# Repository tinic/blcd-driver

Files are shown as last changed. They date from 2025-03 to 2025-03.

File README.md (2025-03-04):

# bldc-driver
Motor driver for brushless dc air conditioner motors

This is a PCB design for readily available adjustable brushless motors used in air conditioning units. These units are great since they are sealed and have ajustable speed while using very little power. I used them to drive a stirrer motor to replace the misspecced AC motors (model YYS6-2/110V/60Hz/0.15A) on the otherwise amazing KOMOS KRYO Inline Draft Beer Chillers which tend to fail quickly and generate extreme amounts of heat (~158F/70C measured). Power consumption is reduced from ~17W to around ~4W for my application while staying _completely_ cool. Torque is ecxellent but not exessive in case of obstructions.

The following units have been tested:

140VDC rated (on 120VAC power):
- ZKFP-20-8-113

310VDC rated (on 240VAC power):
- WZDK30-38G

Notes:
- While these units are rated 140/310VDC they work fine with regular rectified AC power (170/338VDC) which makes the implementation simple/cheap.
- The parts used here are complete overkill as this is not designed for mass manufacturing and the price difference with cheaper parts was negligible in single digit units (~$20 with the DigiKey BOM).
- The only special part here is the 15V DC/DC converter as using a couple of LDOs for this application would have caused excessive power use and heat. A constant current source like a capacitive dropper would not have worked either as the power consumption by these motors on the 15V rail is not constant.
- The PCB was designed to stay under 100x100mm to take advantage of flat price of $5 PCBWay offers for these sizes.

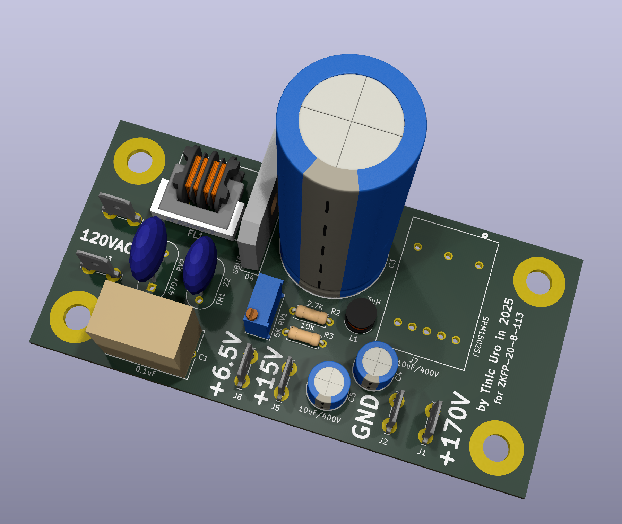
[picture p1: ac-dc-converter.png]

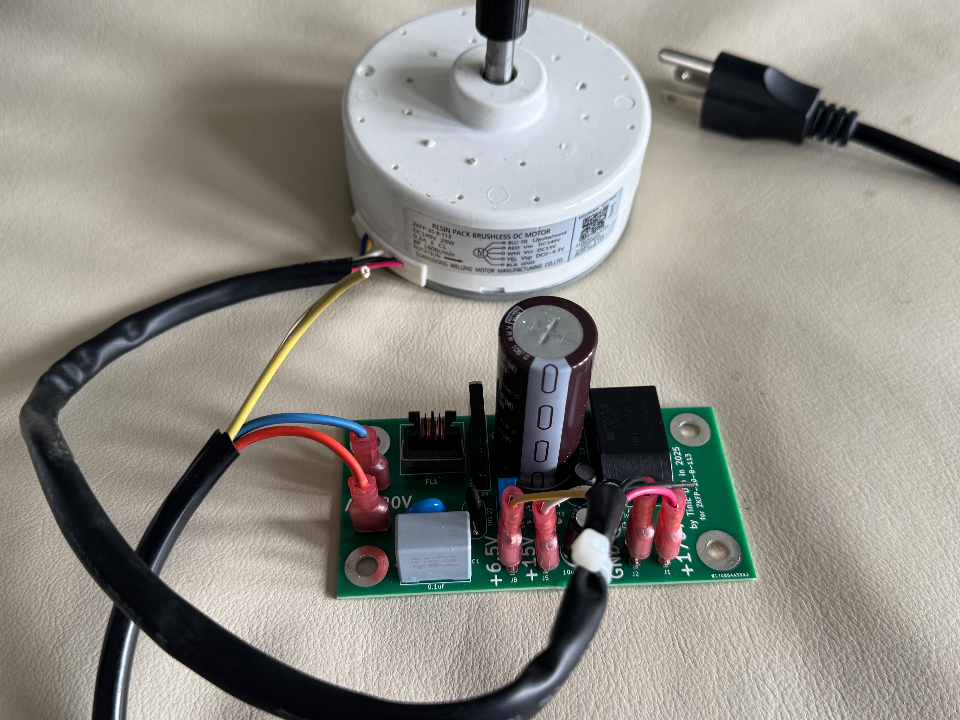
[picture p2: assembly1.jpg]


New motor installed in the beer chiller:

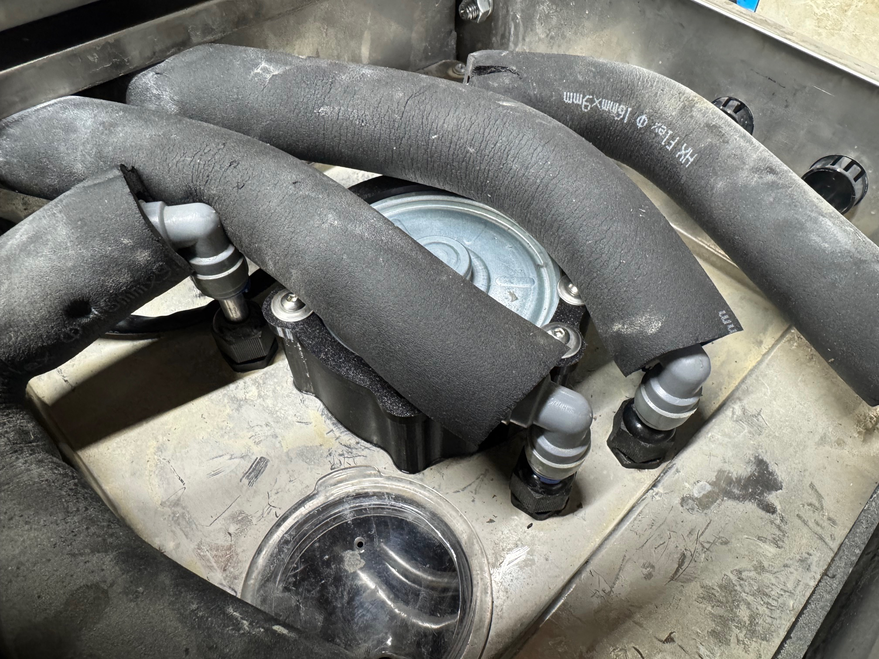
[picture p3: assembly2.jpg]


New stirrer motor with 3d printed blade on the left, old one on the right:

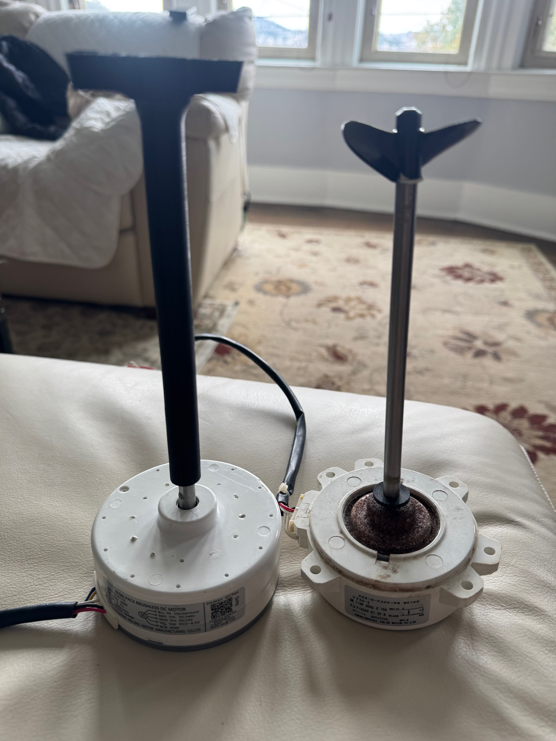
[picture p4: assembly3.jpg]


The push in fittings were completely cooked by the old motor:

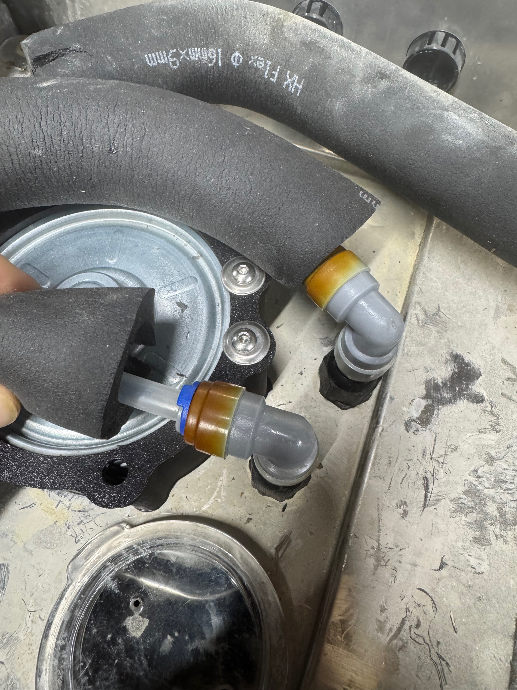
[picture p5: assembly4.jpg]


Full assembly of the new motor in the chiller, the new PCB is on the bottom right:

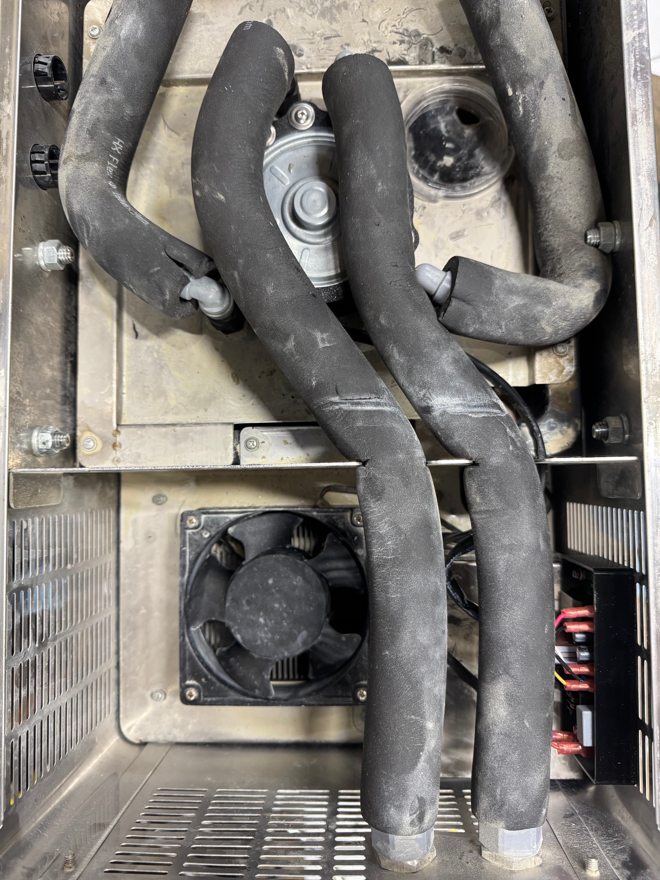
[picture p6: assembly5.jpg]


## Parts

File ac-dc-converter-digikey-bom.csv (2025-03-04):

Country of Origin may be different at time of shipment.
The HTSUS and ECCN information shown is for informational purposes only and is not a representation or warranty as to the accuracy or reliability of these classifications. All information is provided "as is" and is subject to change without notice. Any use made of the information provided is without recourse to Digi-Key and at the user's risk.
Index | Manufacturer Part Number | Manufacturer Name | Description | Availability | Stock Status | Attrition % | Requested Quantity 1 | Pack Quantity 1 | Pack Type 1 | Digi-Key Part Number 1 | Unit Price 1 | Extended Price 1 | Minimum Order Quantity 1 | Customer Reference | Requested Part Number | Lead Weeks | Datasheet | Reference Designator | US Import Tariff | Note | Part Status | RoHS Status | Moisture Sensitivity Level (MSL) | ECCN | HTSUS | Country of Origin | Environmental Information | Original Part numbers | Image | Product Notes
1 | SPM1502SJ | Tamura | DC DC CONVERTER 15V 4W | 301 | In Stock |  | 1 | 1 | Bulk | MT7389-ND | 5.26000 | $5.26 | 1 |  | SPM1502SJ | 26 | https://www.tamuracorp.com/electronics/pdf/EN/SPM/SPM1502SJ_1509CE.pdf |  | May apply on shipments to the U.S. |  | Active | RoHS Compliant | 1 (Unlimited) | EAR99 | 8504.40.9580 | China |  | SPM1502SJ | https://mm.digikey.com/Volume0/opasdata/d220001/medias/images/993/SPM1203SJ.JPG
2 | 400AX10MEFC8X16 | Rubycon | CAP ALUM 10UF 20% 400V RADIAL TH | 3,850 | In Stock |  | 2 | 2 | Bulk | 1189-3119-ND | 0.74000 | $1.48 | 1 |  | 400AX10MEFC8X16 | 16 | https://www.rubycon.co.jp/wp-content/uploads/catalog-aluminum/AX.pdf |  | - |  | Active | ROHS3 Compliant | Not Applicable | EAR99 | 8532.22.0020 | Japan |  | 400AX10MEFC8X16 | https://mm.digikey.com/Volume0/opasdata/d220001/medias/images/1284/AX-SERIES-8x18mm.jpg
3 | 726386-2 | TE Connectivity AMP Connectors | CONN QC TAB 0.250 SOLDER | 38,617 | In Stock |  | 6 | 6 | Bulk | A114371-ND | 0.22000 | $1.32 | 1 |  | 726386-2 | 9 | https://www.te.com/usa-en/product-726386-2.datasheet.pdf |  | - |  | Active | ROHS3 Compliant | 1 (Unlimited) | EAR99 | 8536.90.4000 | Switzerland | http://www.te.com/commerce/alt/SinglePartSearch.do?PN=726386-2&dest=stmt | 726386-2 | https://mm.digikey.com/Volume0/opasdata/d220001/medias/images/29/726386-2.JPG
4 | GBU6M | Diotec Semiconductor | BRIDGE RECT 1PHASE 1KV 4.2A GBU | 884 | In Stock |  | 1 | 1 | Bulk | 4878-GBU6M-ND | 0.83000 | $0.83 | 1 |  | 4878-GBU6M-ND | 2 | https://diotec.com/request/datasheet/gbu6a.pdf |  | May apply on shipments to the U.S. |  | Active | Not applicable | Not Applicable | EAR99 | 8541.10.0080 | China | https://diotec.com/request/imds/p28_e.pdf | 4878-GBU6M-ND | https://mm.digikey.com/Volume0/opasdata/d220001/medias/images/4849/MFG_2796_GBU4A.jpg
5 | MOV-10D471K | Bourns Inc. | VARISTOR 470V 2.5KA DISC 10MM | 66,408 | In Stock |  | 1 | 1 | Bulk | 118-MOV-10D471K-ND | 0.49000 | $0.49 | 1 |  | MOV-10D471K | 13 | https://www.bourns.com/docs/Product-Datasheets/MOV10D.pdf |  | May apply on shipments to the U.S. |  | Active | ROHS3 Compliant | 1 (Unlimited) | EAR99 | 8533.40.4000 | China | https://www.bourns.com/docs/Product-MDS/MOV-10DxxxK.pdf|https://www.bourns.com/docs/rohs-content/bourns-reach-letter.pdf|https://www.bourns.com/docs/rohs-cofc/gmov_cofc.pdf?sfvrsn=c25579f6_4 | MOV-10D471K | https://mm.digikey.com/Volume0/opasdata/d220001/medias/images/405/MFG_MOV-10.jpg
6 | BFC233810104 | Vishay Beyschlag/Draloric/BC Components | CAP FILM 0.1UF 20% 1KVDC RADIAL | 9,153 | In Stock |  | 1 | 1 | Bulk | BC1575-ND | 1.30000 | $1.30 | 1 |  | BFC233810104 | 16 | https://www.vishay.com/docs/28116/mkp3381x1.pdf |  | - |  | Active | ROHS3 Compliant | Not Applicable | EAR99 | 8532.25.0020 | India |  | BFC233810104 | https://mm.digikey.com/Volume0/opasdata/d220001/medias/images/2573/MKP%20338.jpg
7 | SU9HF-07015 | KEMET | CMC 1.5MH 700MA 2LN TH | 773 | In Stock |  | 1 | 1 | Tray | 399-SU9HF-07015-ND | 0.96000 | $0.96 | 1 |  | SU9HF-07015 | 33 | https://search.kemet.com/download/datasheet/SU9HF-07015 |  | - |  | Active | ROHS3 Compliant | Not Applicable | EAR99 | 8504.50.8000 | Vietnam |  | SU9HF-07015 | https://mm.digikey.com/Volume0/opasdata/d220001/medias/images/535/SU9V.jpg
8 | MF72-022D7 | Cantherm | ICL 22 OHM 20% 600MA 9MM | 19,910 | In Stock |  | 1 | 1 | Bulk | 317-1153-ND | 0.43000 | $0.43 | 1 |  | MF72-022D7 | 8 | https://www.cantherm.com/wp-content/uploads/2018/08/MF72_AUG_2018.pdf |  | May apply on shipments to the U.S. |  | Active | ROHS3 Compliant | Not Applicable | EAR99 | 8533.40.8070 | China | https://www.cantherm.com/wp-content/uploads/2017/05/RoHS-3-English-2015-863-EU-SEP-18-2019.pdf | MF72-022D7 | https://mm.digikey.com/Volume0/opasdata/d220001/medias/images/929/MF72-022D7.JPG
9 | EKMM401VSN221MP50S | Chemi-Con | CAP ALUM 400V POLAR | 388 | In Stock |  | 1 | 1 | Bulk | 565-EKMM401VSN221MP50S-ND | 5.43000 | $5.43 | 1 |  | EKMM401VSN221MP50S | 18 | https://www.chemi-con.co.jp/products/relatedfiles/capacitor/catalog/KMMN-e.PDF |  | - |  | Active | ROHS3 Compliant | Not Applicable | EAR99 | 8532.22.0040 | Japan |  | EKMM401VSN221MP50S | https://mm.digikey.com/Volume0/opasdata/d220001/medias/images/3603/EKMGXXXELLXXXMHBXD.jpg
10 | 3296W-1-502LF | Bourns Inc. | TRIMMER 5K OHM 0.5W PC PIN TOP | 514 | In Stock |  | 1 | 1 | Tube | 3296W-502LF-ND | 2.05000 | $2.05 | 1 |  | 3296W-502LF-ND | 10 | https://www.bourns.com/docs/product-datasheets/3296.pdf |  | - |  | Active | ROHS3 Compliant | Not Applicable | EAR99 | 8533.40.8050 | Costa Rica | https://www.bourns.com/docs/rohs-cofc/cofc_trim1.pdf?sfvrsn=ec972807_4 | 3296W-502LF-ND | https://mm.digikey.com/Volume0/opasdata/d220001/medias/images/2383/3296W%20SERIES.jpg
11 | MFR-25FRF52-10K | YAGEO | RES 10K OHM 1% 1/4W AXIAL | 374,500 | In Stock |  | 1 | 1 | Cut Tape (CT) | 13-MFR-25FRF52-10KCT-ND | 0.10000 | $0.10 | 1 |  | 13-MFR-25FRF52-10KTR-ND | 16 | https://www.yageo.com/upload/media/product/app/datasheet/lr/yageo-mfr_datasheet.pdf |  | May apply on shipments to the U.S. |  | Active | ROHS3 Compliant | Not Applicable | EAR99 | 8533.21.0090 | China |  | 13-MFR-25FRF52-10KTR-ND | https://mm.digikey.com/Volume0/opasdata/d220001/medias/images/1206/MFR-25FRF52-10K.jpg
12 | RNMF14FTC2K70 | Stackpole Electronics Inc | RES 2.7K OHM 1% 1/4W AXIAL | 18,090 | In Stock |  | 1 | 1 | Cut Tape (CT) | S2.7KCACT-ND | 0.10000 | $0.10 | 1 |  | S2.7KCATR-ND | 22 | https://www.seielect.com/catalog/sei-rnf_rnmf.pdf |  | May apply on shipments to the U.S. |  | Active | ROHS3 Compliant | Not Applicable | EAR99 | 8533.21.0090 | China | https://www.seielect.com/catalog/SEI-RoHS_Compliance_Status.pdf|https://www.seielect.com/catalog/reach.pdf|https://www.seielect.com/catalog/cert-of-compliance.pdf | S2.7KCATR-ND | https://mm.digikey.com/Volume0/opasdata/d220001/medias/images/2582/RNMF14%202-7k.jpg
13 | DRC-V-3R3M | Signal Transformer | FIXED IND 3.3UH 4.6A 0.025OHM TH | 1,449 | In Stock |  | 1 | 1 | Tray | 595-DRC-V-3R3M-ND | 0.61000 | $0.61 | 1 |  | 595-DRC-V-3R3M-ND | 24 | https://www.belfuse.com:443/resources/datasheets/signaltransformer/ds-ST-DRC-V-series.pdf |  | May apply on shipments to the U.S. |  | Active | ROHS3 Compliant | Not Applicable | EAR99 | 8504.50.8000 | China |  | 595-DRC-V-3R3M-ND | https://mm.digikey.com/Volume0/opasdata/d220001/medias/images/4052/DRC-V-3R3M.jpg

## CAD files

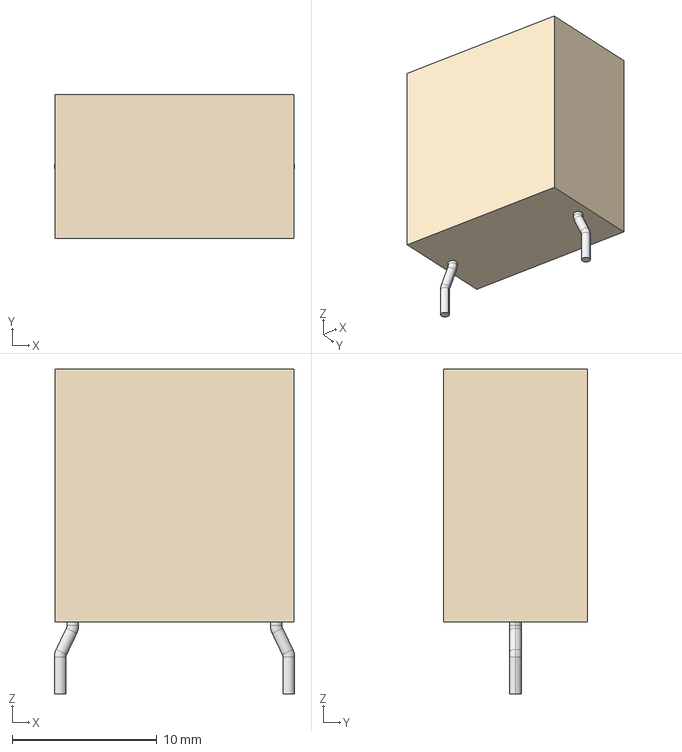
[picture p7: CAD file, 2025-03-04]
ac-dc-converter/models/CAP_17_5X10X16_5_VIS.step
16.6 x 9.98 x 22.5 mm

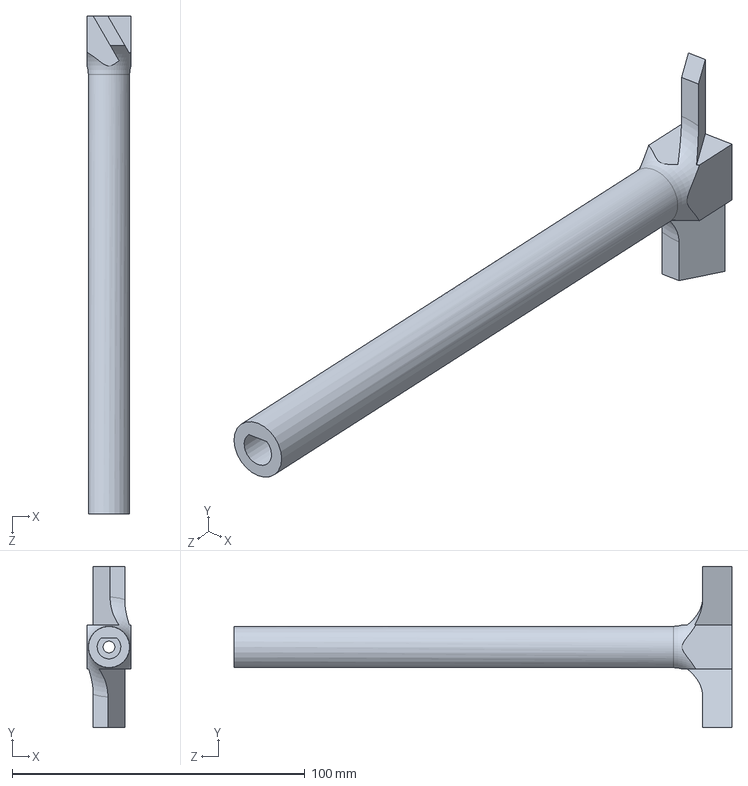
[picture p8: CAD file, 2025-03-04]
komos_kyro/StirrerProp.SLDPRT
15.0 x 55.0 x 170.0 mm

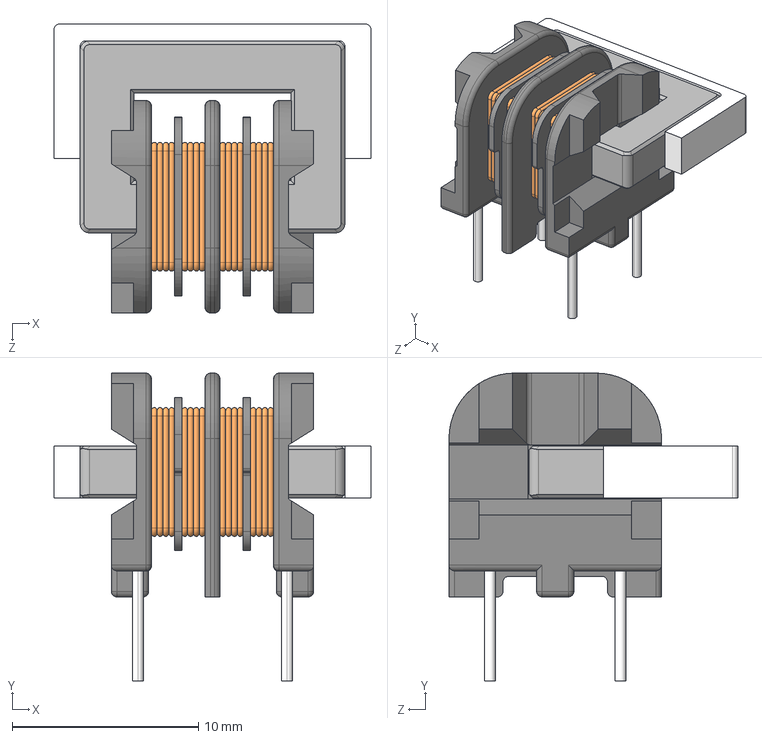
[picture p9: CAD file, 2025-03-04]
ac-dc-converter/models/SU9HF-07015.step
17.0 x 16.5 x 15.5 mm

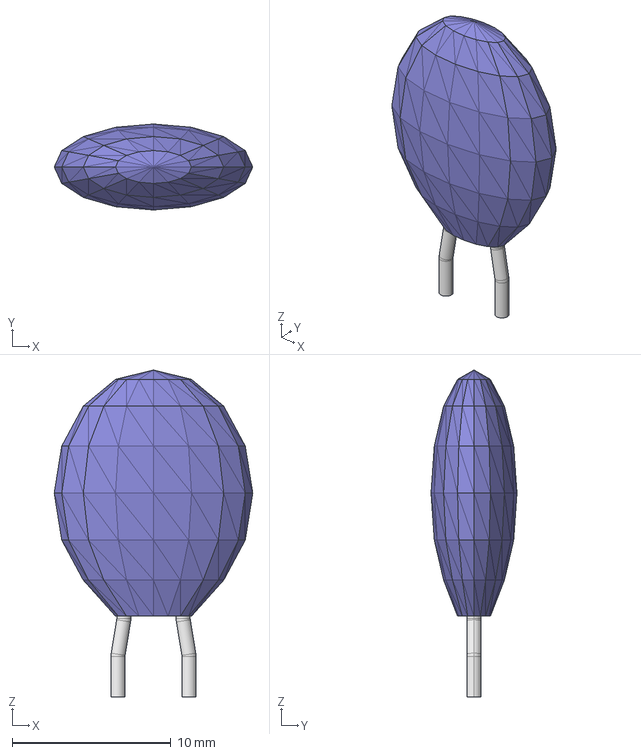
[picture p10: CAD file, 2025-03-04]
ac-dc-converter/models/VAR_MOV-10D471K_BRN.step
12.5 x 5.41 x 20.6 mm

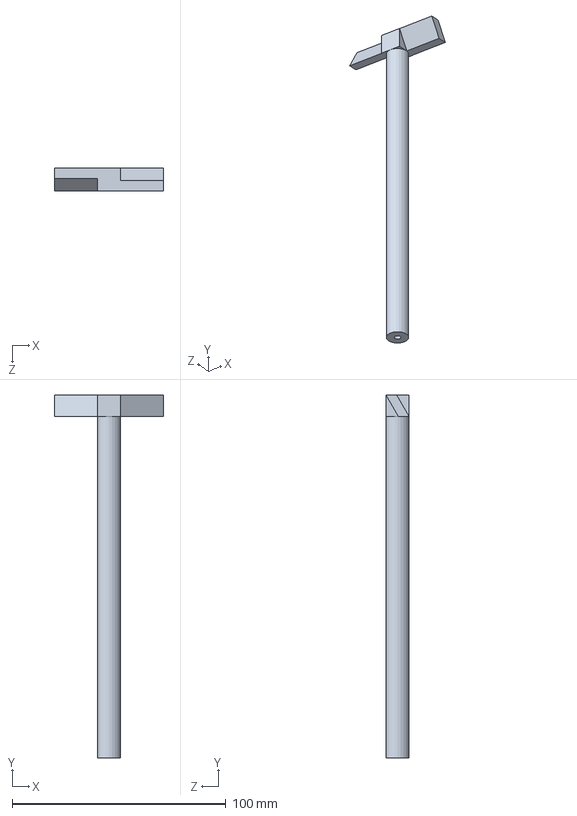
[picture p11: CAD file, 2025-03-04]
komos_kyro/StirrerPropSmall.SLDPRT
51.0 x 170.0 x 11.0 mm

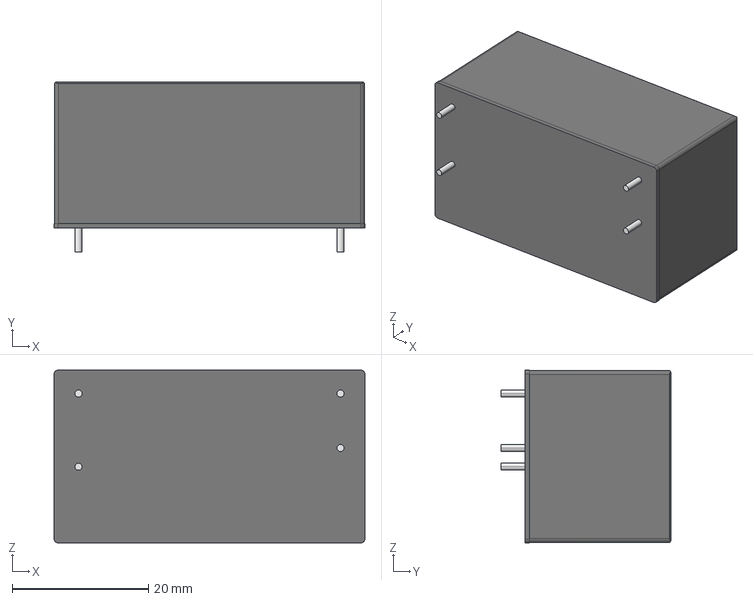
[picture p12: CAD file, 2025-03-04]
ac-dc-converter/models/power_supply_irm-10-15.stp
45.7 x 25.0 x 25.4 mm

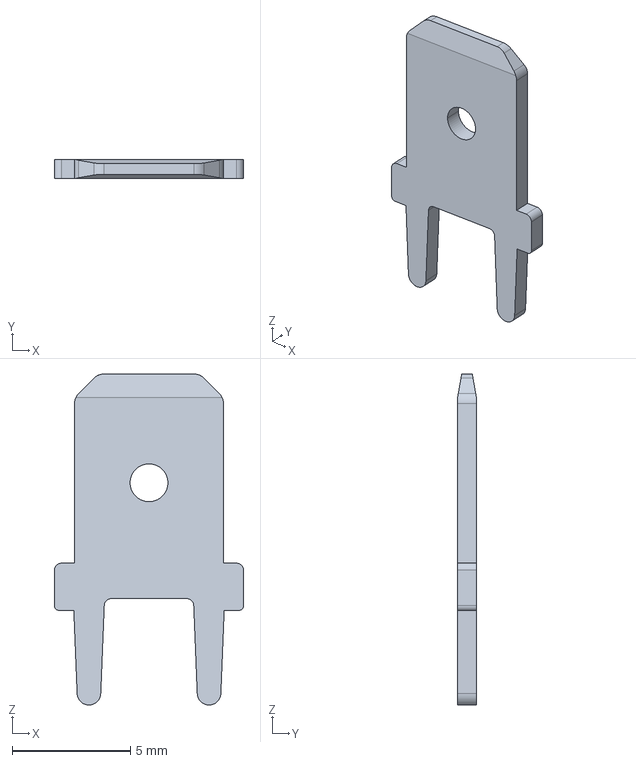
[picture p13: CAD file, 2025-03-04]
ac-dc-converter/models/c-726386-2-g-3d.stp
8.00 x 0.8 x 14.0 mm

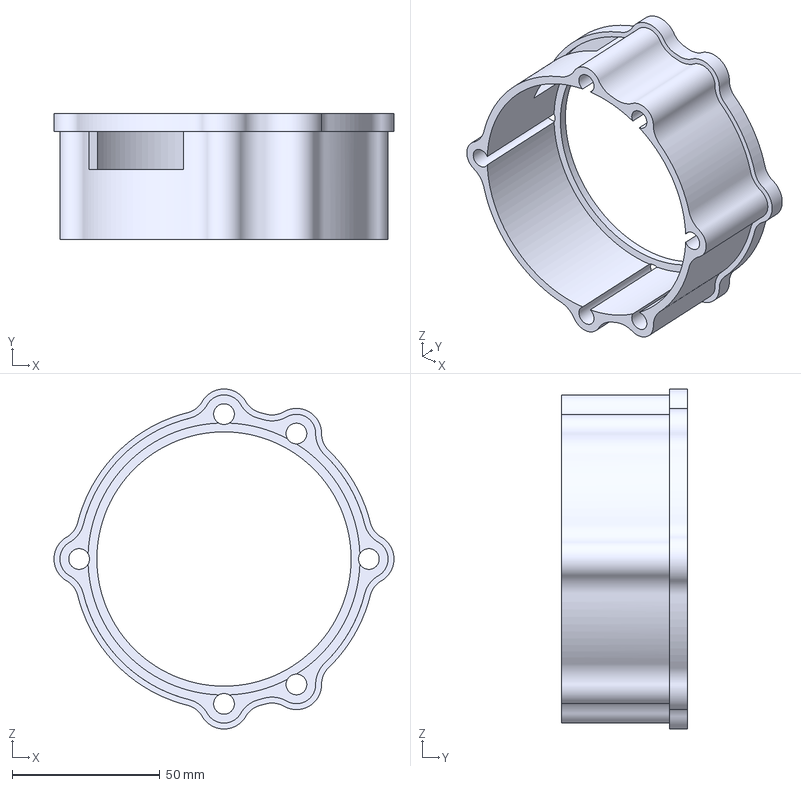
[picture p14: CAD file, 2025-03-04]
komos_kyro/MotorMountV2 - Default.3MF
115.0 x 42.6 x 115.0 mm

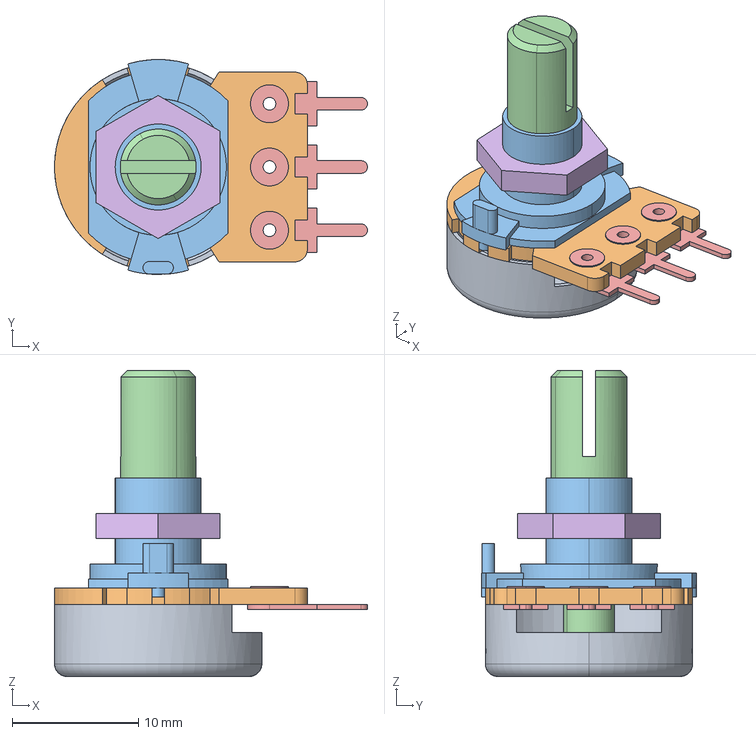
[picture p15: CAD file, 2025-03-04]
ac-dc-converter/models/POT.stp
24.8 x 17.0 x 24.2 mm

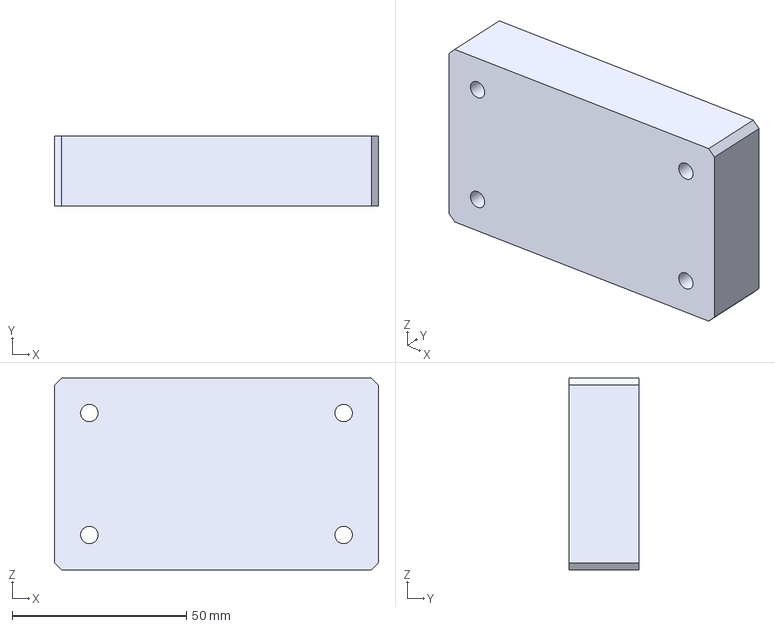
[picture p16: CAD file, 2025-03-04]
komos_kyro/BoardCase - Default.3MF
93.0 x 20.0 x 55.0 mm

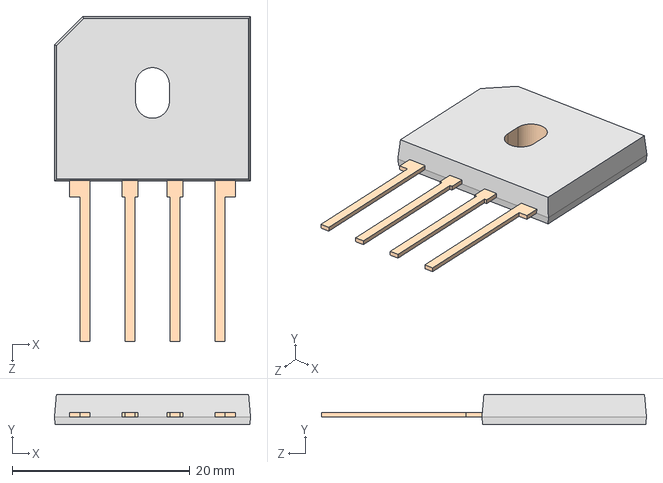
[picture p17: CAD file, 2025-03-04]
ac-dc-converter/models/GBU.step
22.1 x 3.43 x 36.6 mm

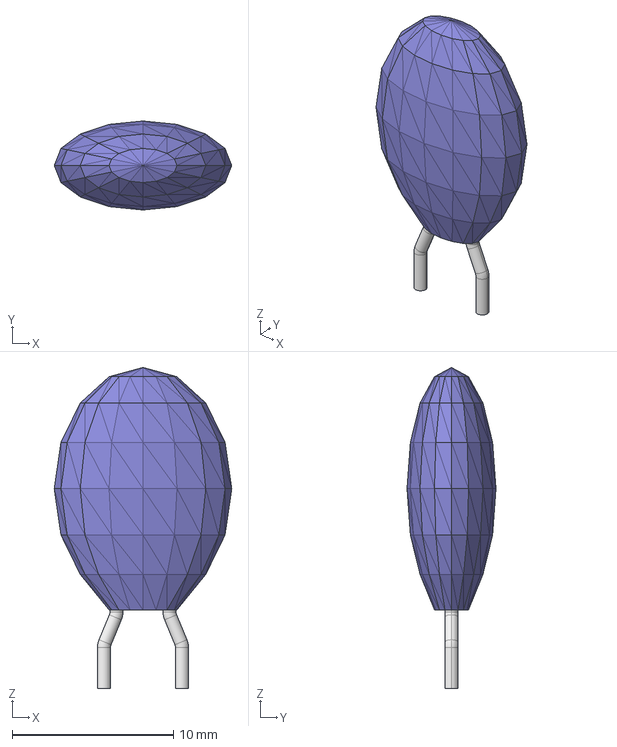
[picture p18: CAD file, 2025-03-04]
ac-dc-converter/models/MF72-010D9_CTM.step
11.0 x 5.51 x 19.9 mm

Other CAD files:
komos_kyro/StirrerProp - Default.3MF
komos_kyro/StirrerPropSmall - Default.3MF
komos_kyro/BoardCase.SLDPRT
komos_kyro/MotorMountV2.SLDPRT

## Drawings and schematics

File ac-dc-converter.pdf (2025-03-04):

# +170V GND

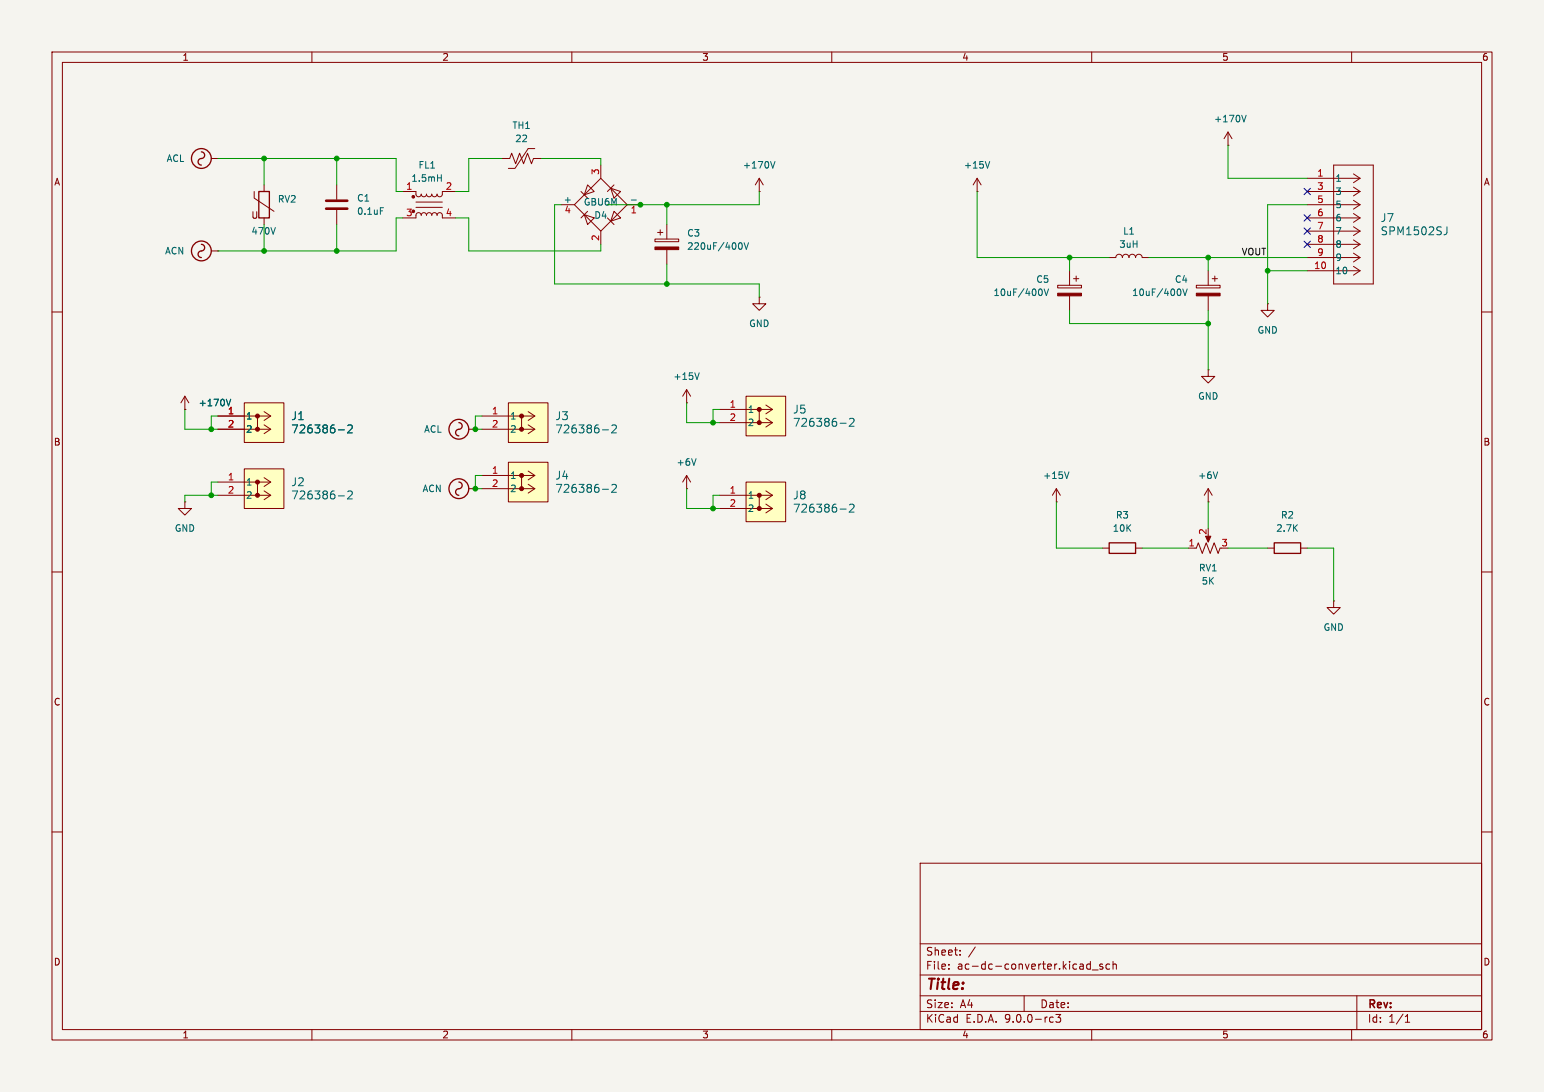
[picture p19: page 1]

Id: 1/1 Title: File: ac-dc-converter.kicad_sch Sheet: /

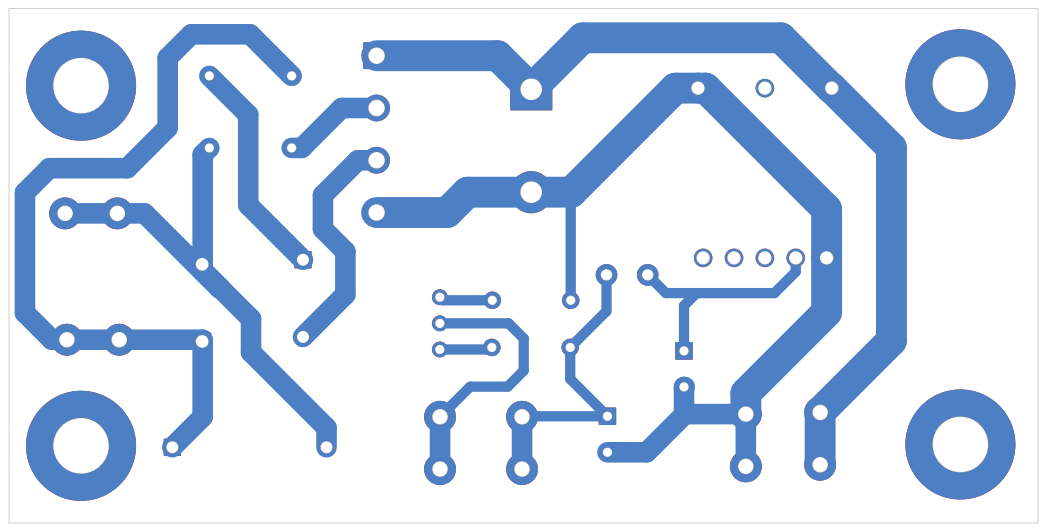
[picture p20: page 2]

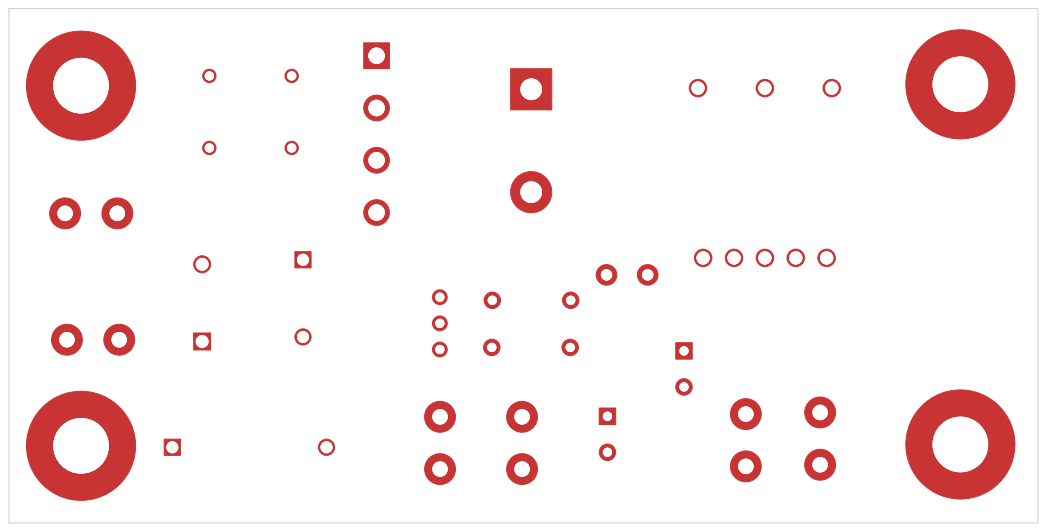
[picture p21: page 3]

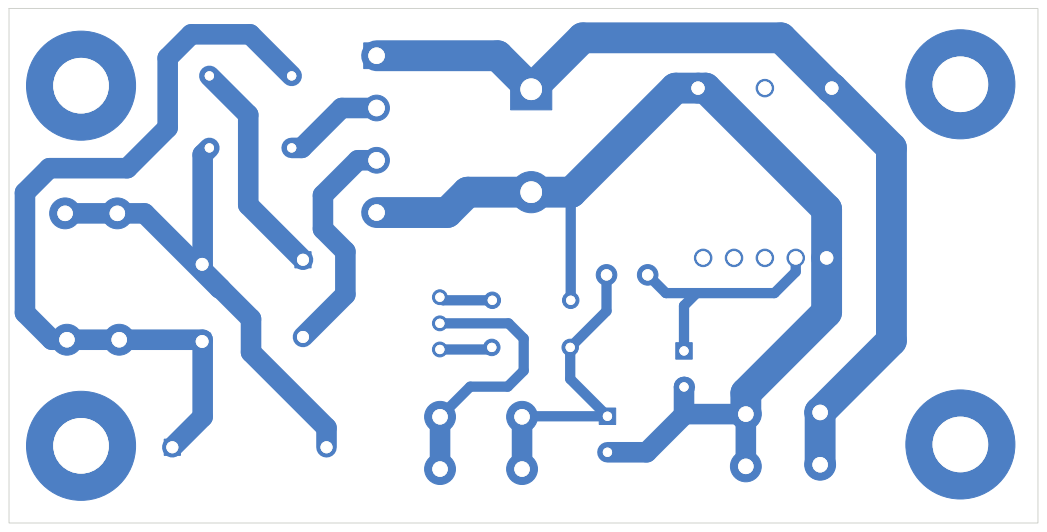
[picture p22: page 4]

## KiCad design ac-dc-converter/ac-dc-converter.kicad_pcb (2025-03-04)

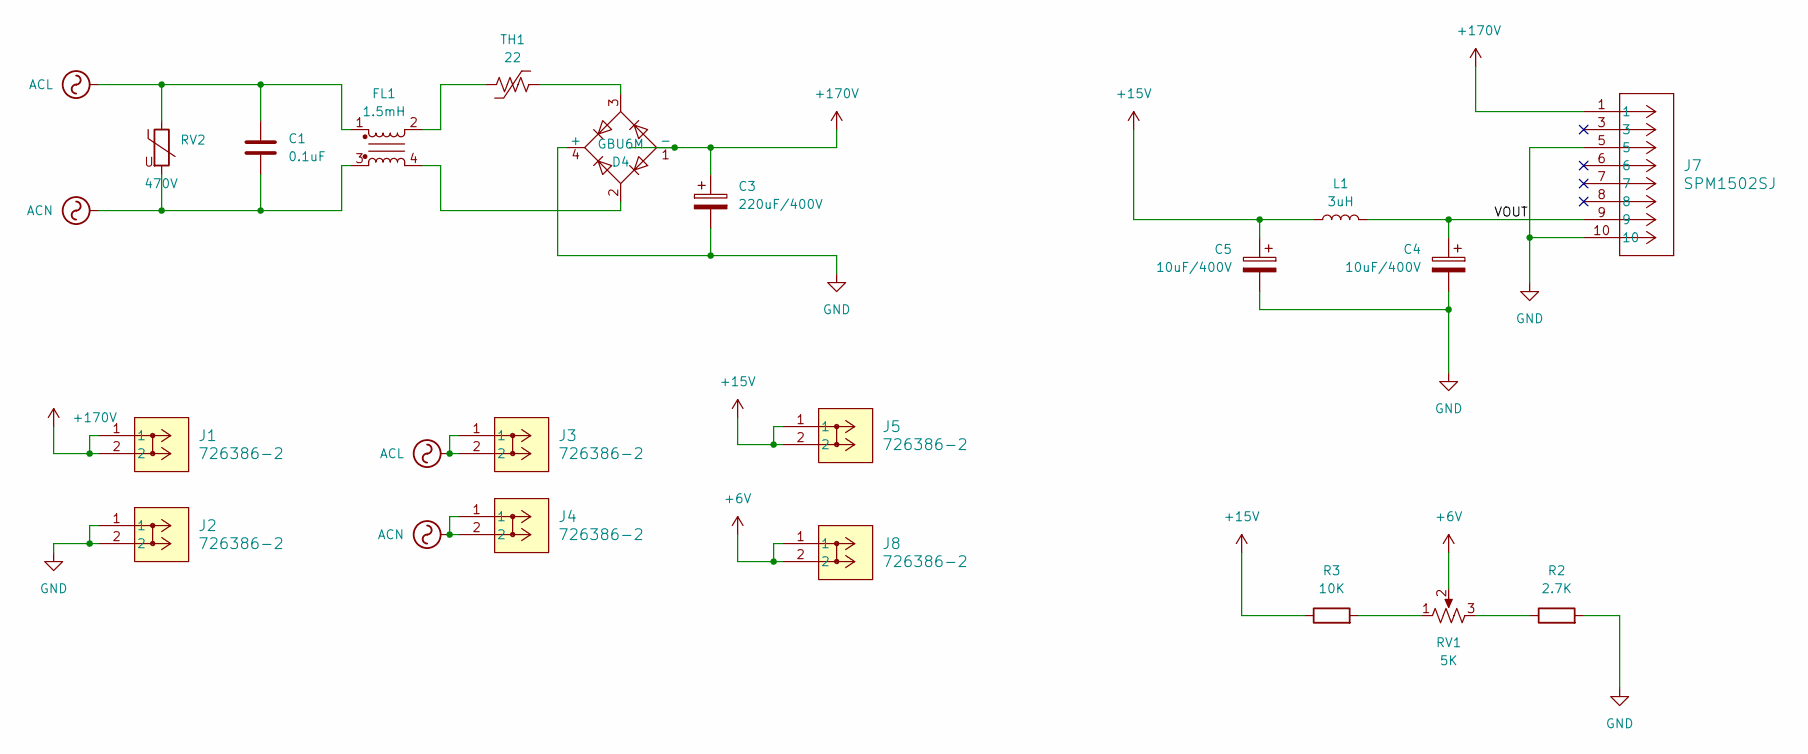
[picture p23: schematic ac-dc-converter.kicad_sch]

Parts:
C1: 0.1uF; CAP_17.5 X 10 X 16.5_VIS; Part BFC233810104
C3: 220uF/400V; CP_Radial_D22.0mm_P10.00mm_SnapIn; Part EKMM401VSN221MP50S
C4, C5: 10uF/400V; CP_Radial_D8.0mm_P3.50mm; Part 400AX10MEFC8X16
D4: GBU6M; RECT_GBU_VIS; Part GBU6M
FL1: 1.5mH; SU9HF07015; Part SU9HF-07015
J1, J2, J3, J4, J5, J8: 726386-2; CONN_726386-2_TEC; Part 726386-2
J7: SPM1502SJ; CONN8_502SJ_TMA; Part SPM1502SJ
L1: 3uH; L_Radial_D6.0mm_P4.00mm; Part DRC-V-3R3M
R2: 2.7K; R_Axial_DIN0207_L6.3mm_D2.5mm_P7.62mm_Horizontal; Part RNMF14FTC2K70
R3: 10K; R_Axial_DIN0207_L6.3mm_D2.5mm_P7.62mm_Horizontal; Part MFR-25FRF52-10K
RV1: 5K; Potentiometer_Bourns_3296W_Vertical; Part 3296W-1-502LF
RV2: 470V; VAR_MOV-10D471K_BRN; Part MOV-10D471K
TH1: 22; MF72-010D9_CTM; Part MF72-022D7

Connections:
+6V: J8.1, J8.2, RV1.2
+15V: C5.1, J5.1, J5.2, L1.2, R3.1
+170V: C3.1, D4.1 (-), J1.1, J1.2, J7.1
/VOUT: C4.1, J7.9, L1.1
ACL: C1.1, FL1.1, J3.1, J3.2, RV2.1
ACN: C1.2, FL1.3, J4.1, J4.2, RV2.2
GND: C3.2, C4.2, C5.2, D4.4 (+), J2.1, J2.2, J7.5, J7.10, R2.2
unnamed: D4.2, FL1.4
unnamed: D4.3, TH1.2
unnamed: FL1.2, TH1.1
unnamed: R2.1, RV1.3
unnamed: R3.2, RV1.1

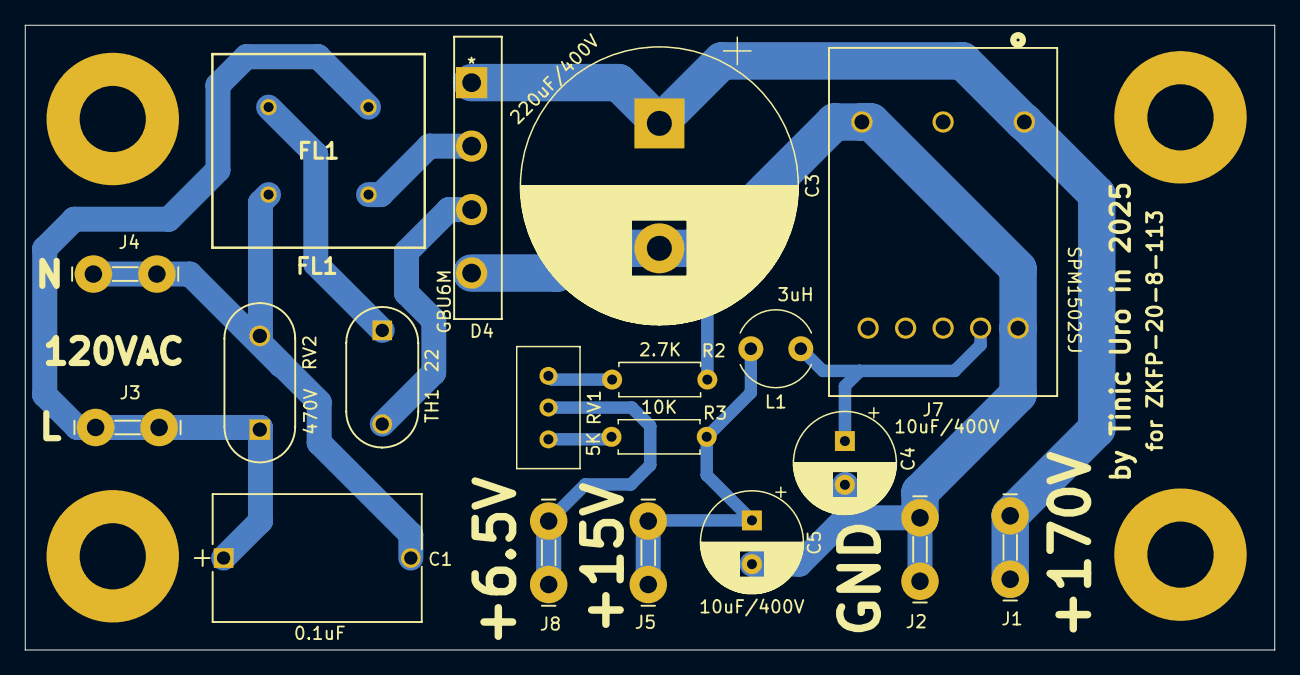
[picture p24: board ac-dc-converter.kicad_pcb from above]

Board: 2 copper layers, 100.0 x 50.0 mm, 19 parts (0 on the bottom side), 12 nets.
